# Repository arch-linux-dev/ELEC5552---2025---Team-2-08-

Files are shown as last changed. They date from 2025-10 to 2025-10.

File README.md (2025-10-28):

# ELEC5552 - 2025 - Team-2-08
Open-source Indoor Surveillance Drone by UWA Team 2-08 for ELEC5552. Includes hardware, firmware and software. Designed for safe indoor flight, testing, and future open-source development.

# FC
## Specifications
Two-layer custom Flight Controller PCB designed in Altium. Integrates ESP32-WROOM-32E microcontroller, ICM-42670P IMU, ultrasonic and IR sensor interfaces, and a 10-pin JST connector for ESC communication. Operates on 3.3 V logic and 5 V sensor input, with regulated power, compact form factor, and mounting compatibility with the drone chassis.
## Images


Top layer view of the Flight Controller PCB showing component layout and routing.



Bottom layer (ground plane) view showing grounding and power distribution.



3D rendered view of the completed Flight Controller PCB.

# ESC
## Specifications
Four-layer 4-in-1 Electronic Speed Controller (ESC) PCB integrating buck-boost and 3.3 V regulation stages, current-sense amplifier, STM32 microcontrollers, gate-driver ICs, and low R<sub>DS(on)</sub> MOSFETs for efficient BLDC motor control. Compatible with 1 S 3.7 V 800 mAh Li-Po battery and AM32 firmware. Designed for compactness, low noise, and safe integration within the quadcopter chassis.
## Images


Realistic top and bottom view of the ESC PCB showing component placement and overall layout.



Top, power, ground, and bottom plane views showing component layout and routing.

# Software
## Flight Controller PCB
The flight controller PCB, based on an ESP32 microcontroller with an inbuilt IMU and support for an attached time of flight, radar distance and optical flow sensor.
```
~/FC PCB - Altium Files/
```
The schematic and PCB were designed using Altium, and sent to PCBWay for maunfacturing.
## Electronic Speed Controller PCB
The ESC PCB, which is a four-in-one designed to power all motors of the quadcopter and regulate/distribute power to the flight controller and camera modules.
```
~/ESC PCB - Altium Files/
```
The motor channels are powered by STMicroelectronics MCUs and are intended to run AM32 ESC firmware.
## Flight Controller Firmware - Custom Version (retired)
The original flight controller firmware we intended to use, written in ESP-IDF for an ESP32 using FreeRTOS for scheduling.
```
~/FC Firmware - Version 1/
```
Communication over Wi-Fi using Websockets for data transfer. Complete with a web-based interface for piloting, adjusting PID parameters 'live' without re-writing firmware, and manually overriding setpoints and outputs.
This version was retired as the performance was not adequate for our liking.
## Flight Controller Firmware - Crazyflie Version
A revamped firmware package for our flight controller, this time based on the Crazyflie platform firmware ported to ESP32.
```
~/FC Firmware - Version 2/
```
This package was selected as it had pre-bundled drivers for our peripherals and a much more advanced arsenal of control loops, predictors and situational awareness handlers. 
Many functions were modified or replaced with custom versions to support our hardware and use case. Some of the larger changes include:
* The ESC communication is custom, and was written to translate Crazyflie's motor ratio (a value between 10000 and 60000) into a signal that BLHeli ESCs understand (pulse between 1000ms and 2000ms).
* The time-of-flight sensor drivers were modified to support the initialisation of a second device and address change of one of the devices so they can operate on the same bus simultaneously. 
## Ground Station Python Scripts
These files handle the autonomous navigation step-through, manual control takeover, and video recording via a laptop connected to the drone's Wi-Fi.
### Flight Planner and Manual Control
```
~/Ground Station/planner_interface.py
```
This script allows the planning of a flight path via mouse inputs, clicking points on a grid to set the x,y coordinates for the drone. It communicates these sequentially to the drone. There are also buttons to manually pilot the drone, and cut power when required.
### Video Recording
```
~/Ground Station/cam_handler.py
```
This script, upon launch, opens a stream from the ESP-CAM over the network and encodes it into a .avi file.

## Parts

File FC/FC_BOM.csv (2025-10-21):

Line # | Name | Description | Designator | Quantity | Manufacturer 1 | Manufacturer Part Number 1 | Footprint
 | CL10A226MQ8NRND | Cap Ceramic 22uF 6.3V X5R ±20% Pad SMD 0603 +85°C T/R | C1 | 1 | Samsung Electro-Mechanics | CL10A226MQ8NRND | FP-CL10-IPC_B
 | CAP 100nF 100V 0805(2012) | CAP 100nF 100V ±10% 0805 (2012 Metric) Thickness 1.45mm SMD | C2, C3, C5 | 3 | KEMET | C0805C104K1RACTU | CAPC0805(2012)145_M
 | CC0603KPX5R7BB225 | CC0603 2.2 uF X5R 10.00% 16 V | C6 | 1 | Yageo Group | CC0603KPX5R7BB225 | FP-CC0603-DA-MFG
 | 08056D106KAT4A |  | C7 | 1 | KYOCERA AVX | 08056D106KAT4A | CAPC2013X140X50ML20T25
 | ESP32-WROOM-32E-N8 | WiFi Modules - 802.11 SMD Module ESP32-WROOM-32E, ESP32-D0WD-V3, 8 MB SPI flash, PCB antenna | ESP32 | 1 | Espressif Systems | ESP32-WROOM-32E-N8 | ESP32WROOM32EN8
 | ICM-42670-P | Integrated Circuit | ICM | 1 | TDK | ICM-42670-P | ICM42670P
 | SM10B-SRSS-TB_LF__SN_ | Connector | J1 | 1 | JST | SM10B-SRSS-TB(LF)(SN) | SM10B-SRSS-TB
 | CES-104-02-S-S | Connector | J2, J4 | 2 | Samtec | CES-104-02-S-S | CES-104-XX-Y-S
 | CES-103-01-G-S | Connector | J3 | 1 | Samtec | CES-103-01-G-S | CES-103-XX-Y-S
 | CES-106-01-T-S | Connector | J5 | 1 | Samtec | CES-106-01-T-S | CES-106-XX-Y-S
 | 68001-204HLF | CONN HEADER VERT 4POS 2.54MM | JP1 | 1 | Amphenol Communications Solutions | 68001-204HLF | HDR Male1�~4 2.54mm
 | ERJ-3EKF2401V |  | R1, R4, R5 | 3 | Panasonic | ERJ-3EKF2401V | RESC1608X55X30ML15T15
 | AC0603JR-7W10KL | RES 10kO 5.00% 0.2W 0603 | R2, R3, R6 | 3 | Yageo Group | AC0603JR-7W10KL | FP-AC0603-IPC_A
 | RC1206FR-102KL |  | R7 | 1 | Yageo Group | RC1206FR-102KL | RESC3116X65X40ML10T20
 | RC1206JR-101KL |  | R8 | 1 | Yageo Group | RC1206JR-101KL | RESC3116X65X40ML10T20
 | TL3301AF160QG | SWITCH TACTILE SPST-NO 0.05A 12V | SW1 | 1 | E-Switch | TL3301AF160QG | FP-TL3301AF160QG-MFG
 | TXB0104D | IC TRNSLTR BIDIRECTIONAL 14SOIC | U1 | 1 | Texas Instruments | TXB0104D | FP-D0014A-IPC_A

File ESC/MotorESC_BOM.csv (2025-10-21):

Line # | Name | Description | Designator | Quantity | Manufacturer 1 | Manufacturer Part Number 1 | Supplier 1 | Supplier Part Number 1
 | TPS630701RNMR | IC REG BCK BST 5V 2A 15VQFN | U2 | 1 | Texas Instruments | TPS630701RNMR | Mouser | 595-TPS630701RNMR
 | TPS72733DSER | Single Output Fast Transient Response LDO, 250 mA, Fixed 3.3 V Output, 2 to 5.5 V Input, with Ultra-Low IQ, 6-pin WSON (DSE), -40 to 125 degC, Green (RoHS & no Sb/Br) | U1 | 1 | Texas Instruments | TPS72733DSER | Arrow Electronics | TPS72733DSER
 | T520A107M006ATE045 | CAP TANT POLY 100UF 6.3V 1206 | C26 | 1 | KEMET | T520A107M006ATE045 | Newark | 02AC0118
 | STM32G071GBU6 | IC MCU 32BIT 128KB FLSH 28UFQFPN | U3, U4, U28, U29 | 4 | STMicroelectronics | STM32G071GBU6 | Newark | 84AC2901
 | SM10B-SRSS-TB_LF__SN_ | Connector | J1 | 1 | JST | SM10B-SRSS-TB(LF)(SN) | Mouser | 306-SM10BSRSSTBLFSN
 | SIZ200DT-T1-GE3 | Dual N-Channel 30-V (D-S) MOSFETs Symm. PowerPAIR 3 x 3 1G sh ch , 5.5 m @ 10V m @ 7.5V 7.3 m @ 4.5V | Q1, Q2, Q3, Q4, Q5, Q6, Q7, Q8, Q9, Q10, Q11, Q12 | 12 | Vishay | SIZ200DT-T1-GE3 | Mouser | 78-SIZ200DT-T1-GE3
 | RM2012B-103103-PBVW10 | No Description Available | R12, R13, R24, R25 | 4 | Susumu | RM2012B-103/103-PBVW10 | DigiKey | RM20B10K/10KPCT-ND
 | NCP81161MNTBG | No Description Available | U5, U6, U12, U13, U24, U25, U30, U31, U32, U33, U34, U35 | 12 | onsemi | NCP81161MNTBG | DigiKey | NCP81161MNTBGOSCT-ND
 | MCS04020C1001FE000 | RES SMD 1.2K OHM 1% 1/10W 0402 | R1 | 1 | Vishay | MCS04020C1001FE000 | Newark | 65AC3521
 | INA186A2IDCKT | IC CURR SENSE 1 CIRCUIT SC70-6 | U9 | 1 | Texas Instruments | INA186A2IDCKT | Mouser | 595-INA186A2IDCKT
 | HSMW-C191 |  | D1 | 1 | Avago | HSMW-C191 | Farnell | 1058375
 | HCS1206FTL500 | RES SHUNT, 1206, 0.0005 ohm, 1%, 2W | R9 | 1 | Stackpole Electronics | HCS1206FTL500 | Mouser | 708-HCS1206FTL500
 | GRM188R61E106KA73J | Chip Multilayer Ceramic Capacitors for General Purpose, 0603, 10uF, X5R, 15%, 10%, 25V | C28, C29 | 2 | Murata | GRM188R61E106KA73J | Mouser | 81-GRM188R61E106KA3J
 | GRM155R61A106ME11D | Chip Multilayer Ceramic Capacitors for General Purpose, 0402, 10uF, X5R, 15%, 20%, 10V | C9, C10, C34, C35, C41, C43, C47, C48, C55, C57, C61, C62 | 12 | Murata | GRM155R61A106ME11D | Mouser | 81-GRM155R61A106ME1D
 | GRM21BR61E106MA73L | Chip Multilayer Ceramic Capacitors for General Purpose, 0805, 10uF, X5R, 15%, 20%, 25V | C27 | 1 | Murata | GRM21BR61E106MA73L | Mouser | 81-GRM21BR61E106MA3L
 | GCJ188R71C104MA01D | Cap Ceramic 0.1uF 16V X7R 20% Pad SMD 0603 Soft Termination +125°C Automotive T/R | C31, C32, C39, C40, C45, C46, C53, C54, C59, C60, C65, C66 | 12 | Murata | GCJ188R71C104MA01D | Mouser | 81-GCJ188R71C104MA1D
 | EXB24V102JX | No Description Available | U7, U8, U10, U11 | 4 | Panasonic | EXB-24V102JX | DigiKey | Y5102CT-ND
 | EXB24V100JX | No Description Available | U14, U15, U16, U17, U18, U19, U20, U21, U22, U23, U26, U27 | 12 | Panasonic | EXB-24V100JX | DigiKey | Y5100CT-ND
 | DFE252012F-R82M=P2 | Shielded Wirewound Inductor 0.82uH 20% 3600mA 0.035O 1008 (2520) | L1 | 1 | Murata | DFE252012F-R82M=P2 | Arrow Electronics | DFE252012F-R82M=P2
 | CRG0402F10K | RES SMD 10K OHM 1% 1/16W 0402 | R8, R10, R11, R22, R23 | 5 | TE Connectivity | CRG0402F10K | Newark | 95W7406
 | CAP 10uF 16V 1206(3216) | CAP 10uF 16V -20% to +80% 1206 (3216 Metric) Thickness 1.9mm SMD | C17 | 1 | Yageo Group | CC1206ZKY5V7BB106 | Mouser | 603-CC126ZKY5V7BB106
 | CC0805MKX5R8BB226 | CAP CER 22UF 25V X5R 0805 | C1, C2, C3, C5, C6, C7, C8, C18, C19, C20, C21, C22, C23, C24, C25 | 15 | Yageo Group | CC0805MKX5R8BB226 | Mouser | 603-CC805MKX5R8BB226
 | CAY10-222J4LF | No Description Available | R14, R15, R26, R27 | 4 | Bourns | CAY10-222J4LF | Avnet | 06X4909
 | C0402C103K5RACTU | CAP CER 10000PF 50V X7R 0402 | C38 | 1 | KEMET | C0402C103K5RACTU | Mouser | 80-C0402C103K5R
 | BLM18SG221TN1D | Chip Ferrite Bead, 0603, 220O @ 100MHz, 25%, 0.04O, 2.5A | FB1, FB2 | 2 | Murata | BLM18SG221TN1D | Mouser | 81-BLM18SG221TN1D
 | AC0402FR-7W4K7L | RES 4.7kO ±1% 0.125W 0402 | R2, R3, R4, R5, R6, R7, R16, R17, R18, R19, R20, R21 | 12 | Yageo Group | AC0402FR-7W4K7L | Newark | 59AK0904
 | 12101C225KAZ2A | General Purpose Ceramic Capacitor, 1210, 2.2uF, 10%, X7R, 15%, 100V | C15, C16 | 2 | KYOCERA AVX | 12101C225KAZ2A | Mouser | 581-12101C225KAZ2A
 | 9931-0-00-15-00-00-03-0 | Circuit Board Hardware - PCB STANDARD I.C. PIN | J3, J4, J5, J6, J7, J8, J9, J10, J11, J12, J13, J14 | 12 | Mill-Max | 9931-0-00-15-00-00-03-0 | Mouser | 575-993100150030
 | CAP 100nF 25V 0402(1005) | CAP 100nF 25V ±20% 0402 (1005 Metric) Thickness 0.6mm SMD | C30, C33 | 2 | KYOCERA AVX | 04023D104MAT2A | Mouser | 581-04023D104MAT2A
 | 04023C104JAT2A |  | C11, C12, C13, C14, C36, C37, C42, C44, C49, C50, C51, C52, C56, C58, C63, C64 | 16 | KYOCERA AVX | 04023C104JAT2A | Newark | 96Y8155
 | 741X043222JP | Resistor Networks & Arrays 2.2Kohms 5% Isolated | X1, X2, X3, X4 | 4 | CTS Components | 741X043222JP | Mouser | 774-741X043222JP

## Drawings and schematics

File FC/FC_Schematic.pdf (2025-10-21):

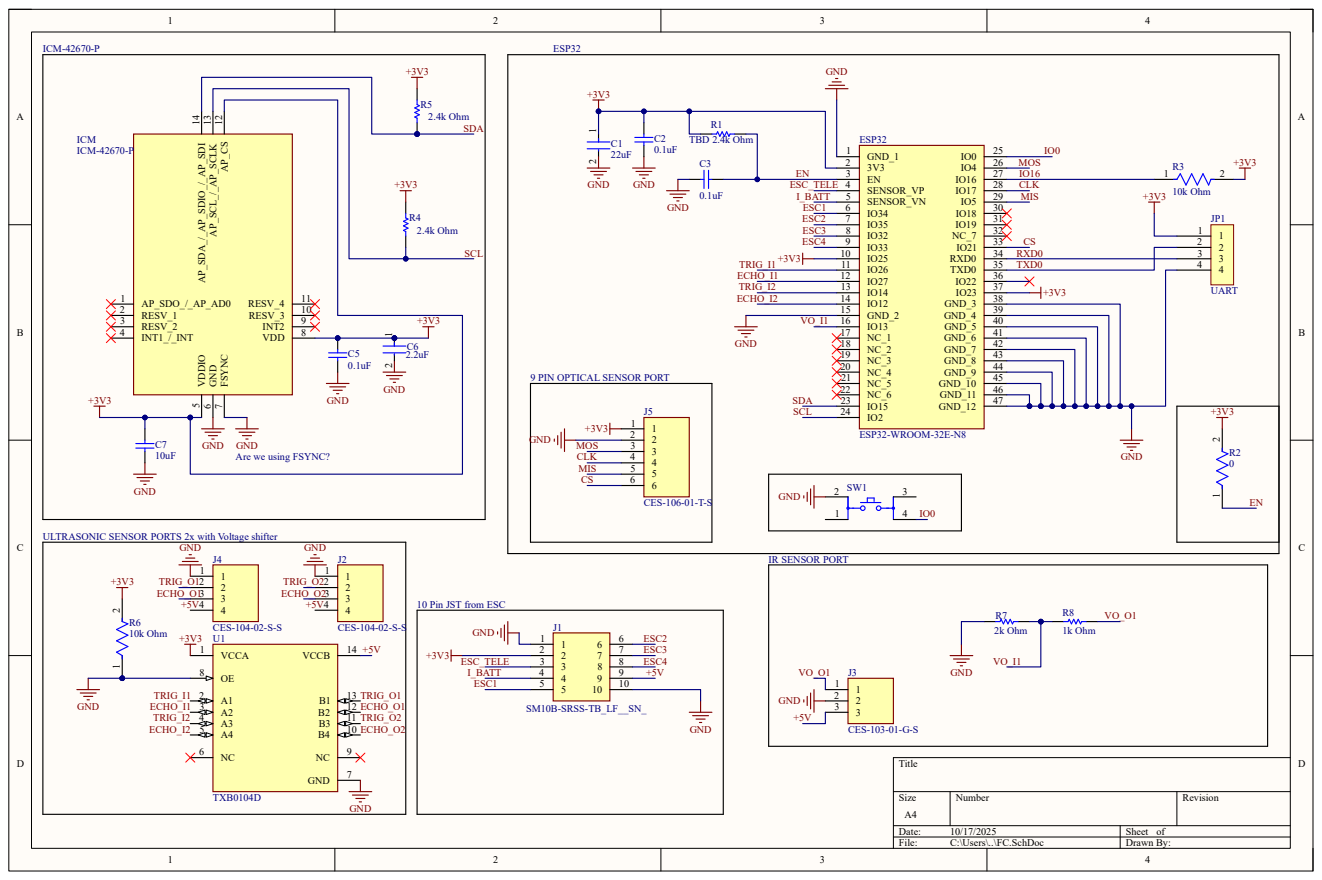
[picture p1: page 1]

9 PIN OPTICAL SENSOR PORT

GND
Are we using FSYNC?

ULTRASONIC SENSOR PORTS 2x with Voltage shifter

10 Pin JST from ESC

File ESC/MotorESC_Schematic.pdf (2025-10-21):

Decoupling Capacitors | Buck-Boost Converter

# GND¹ ²

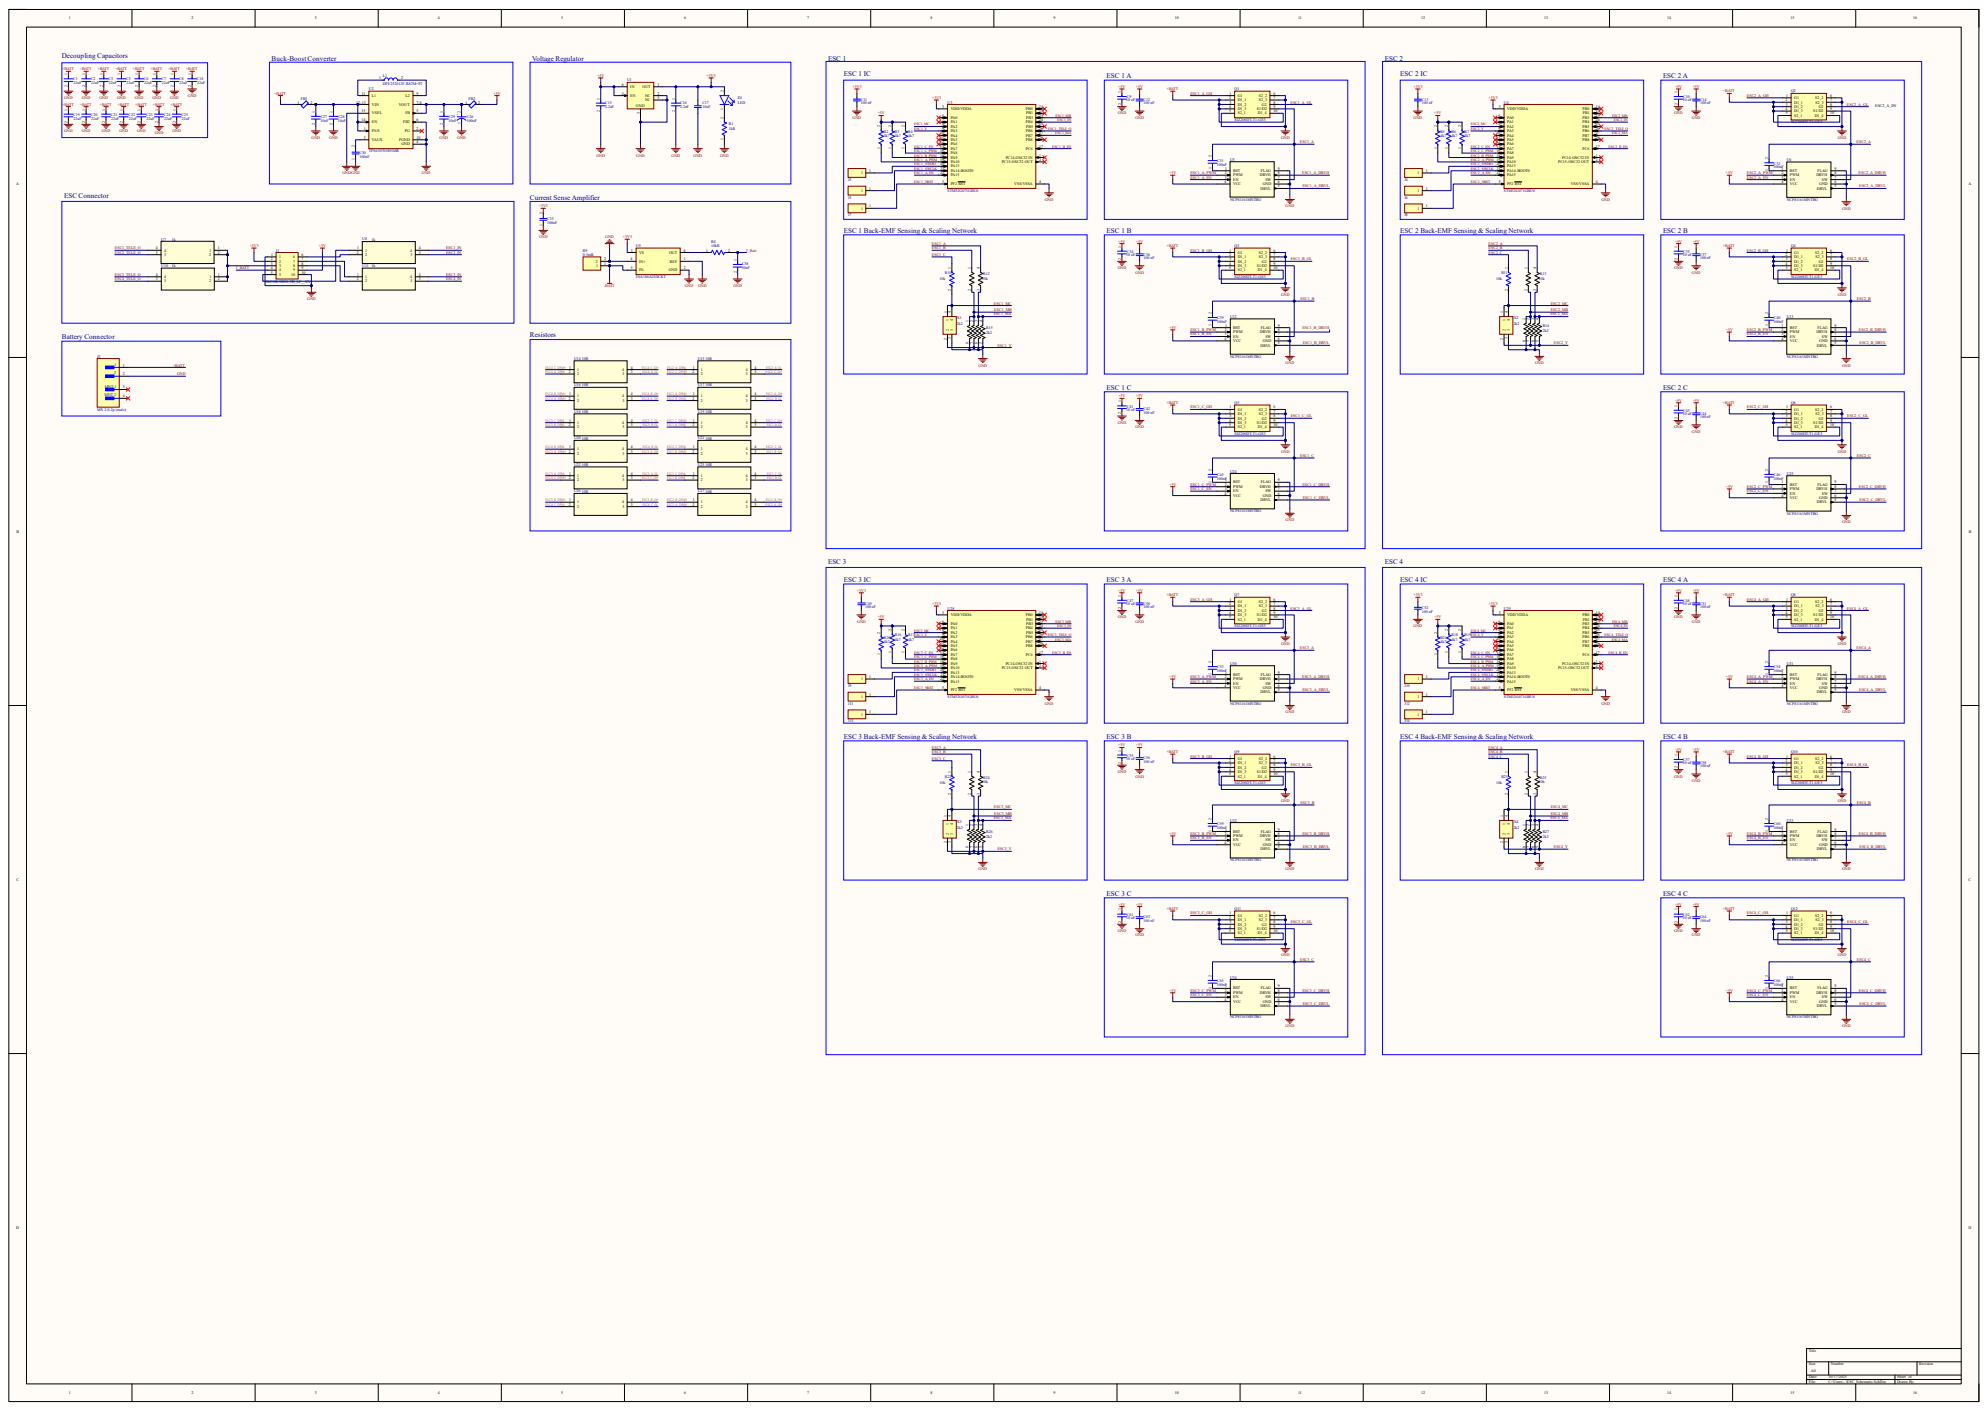
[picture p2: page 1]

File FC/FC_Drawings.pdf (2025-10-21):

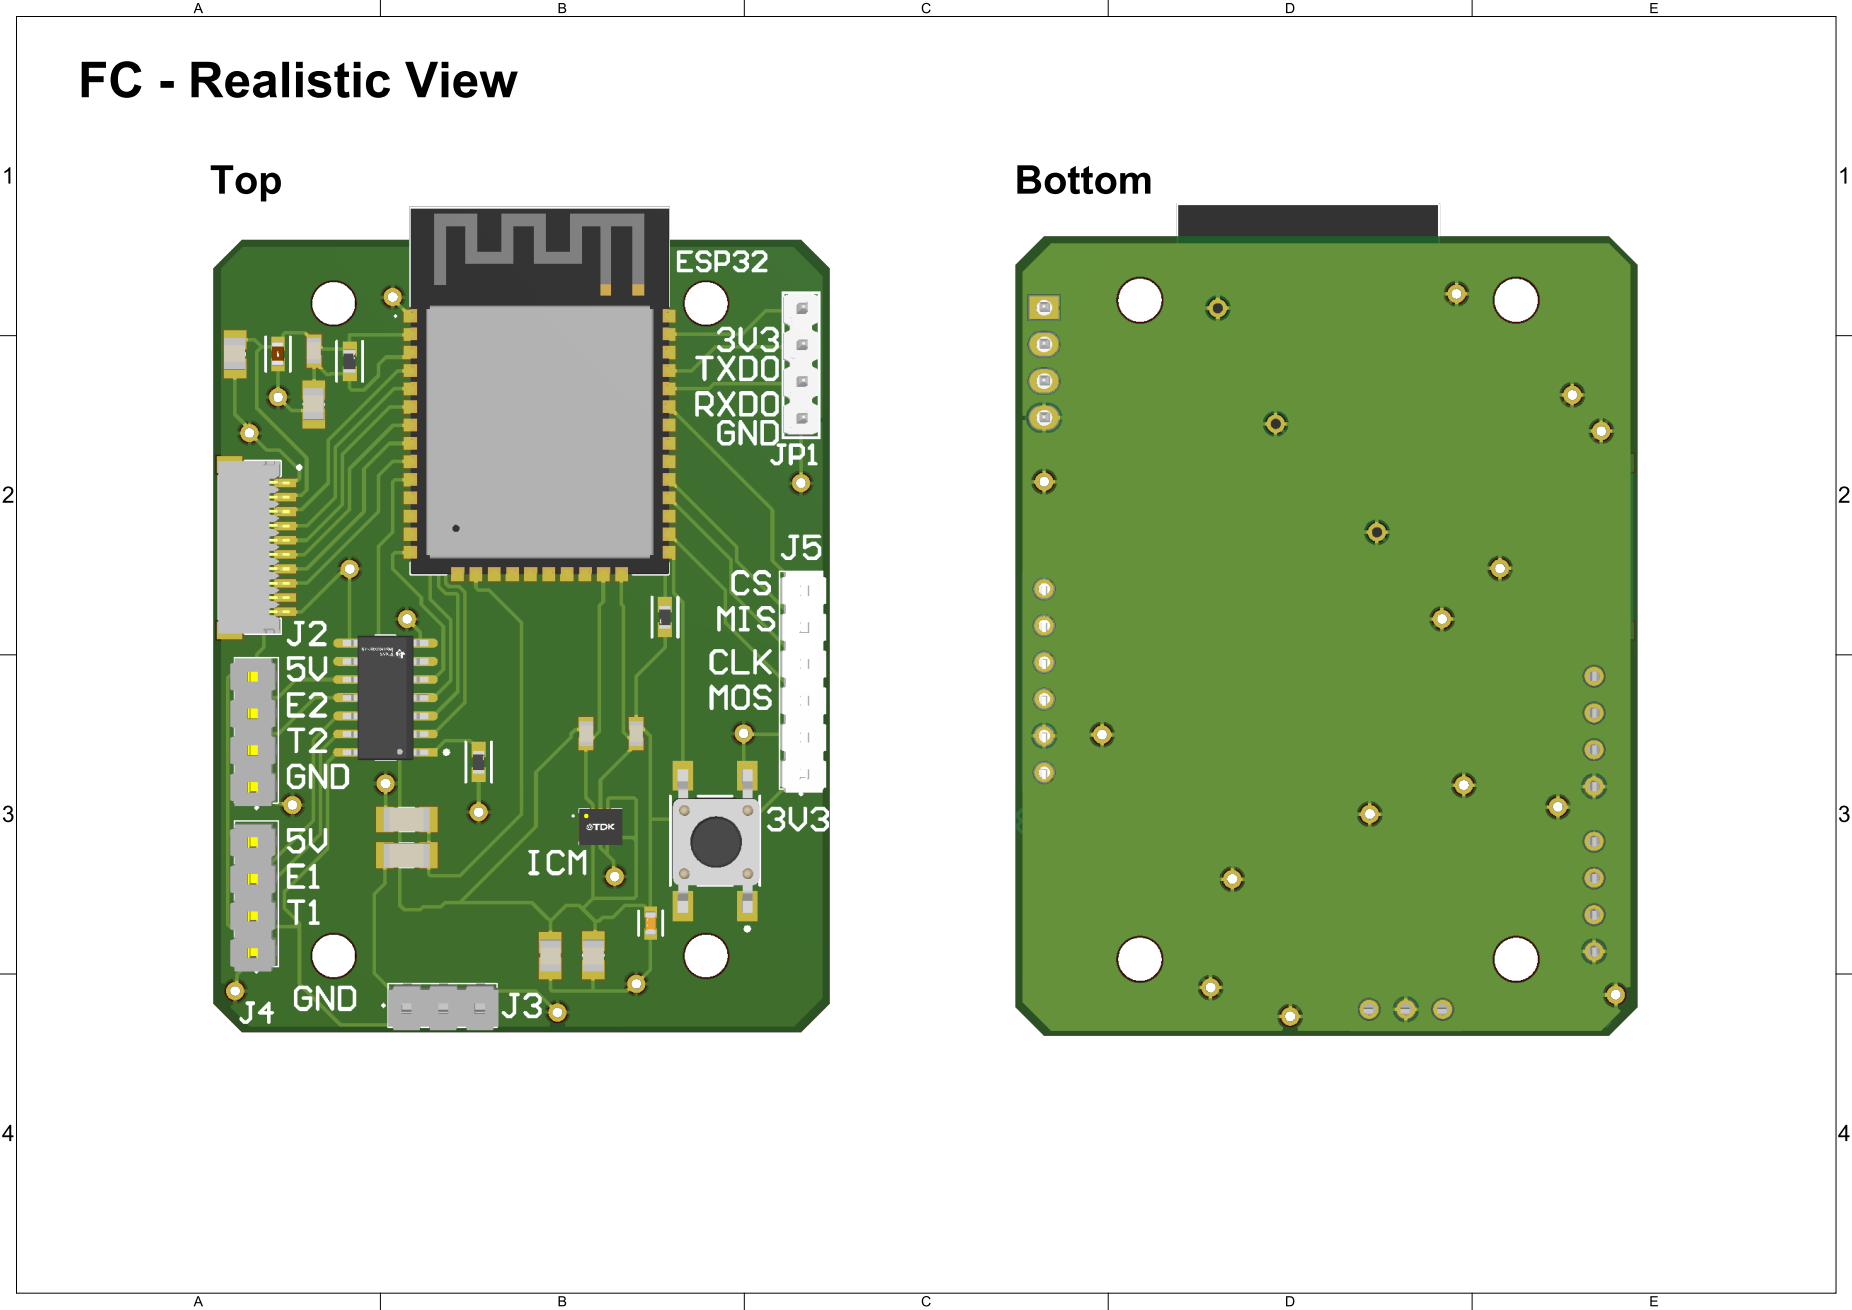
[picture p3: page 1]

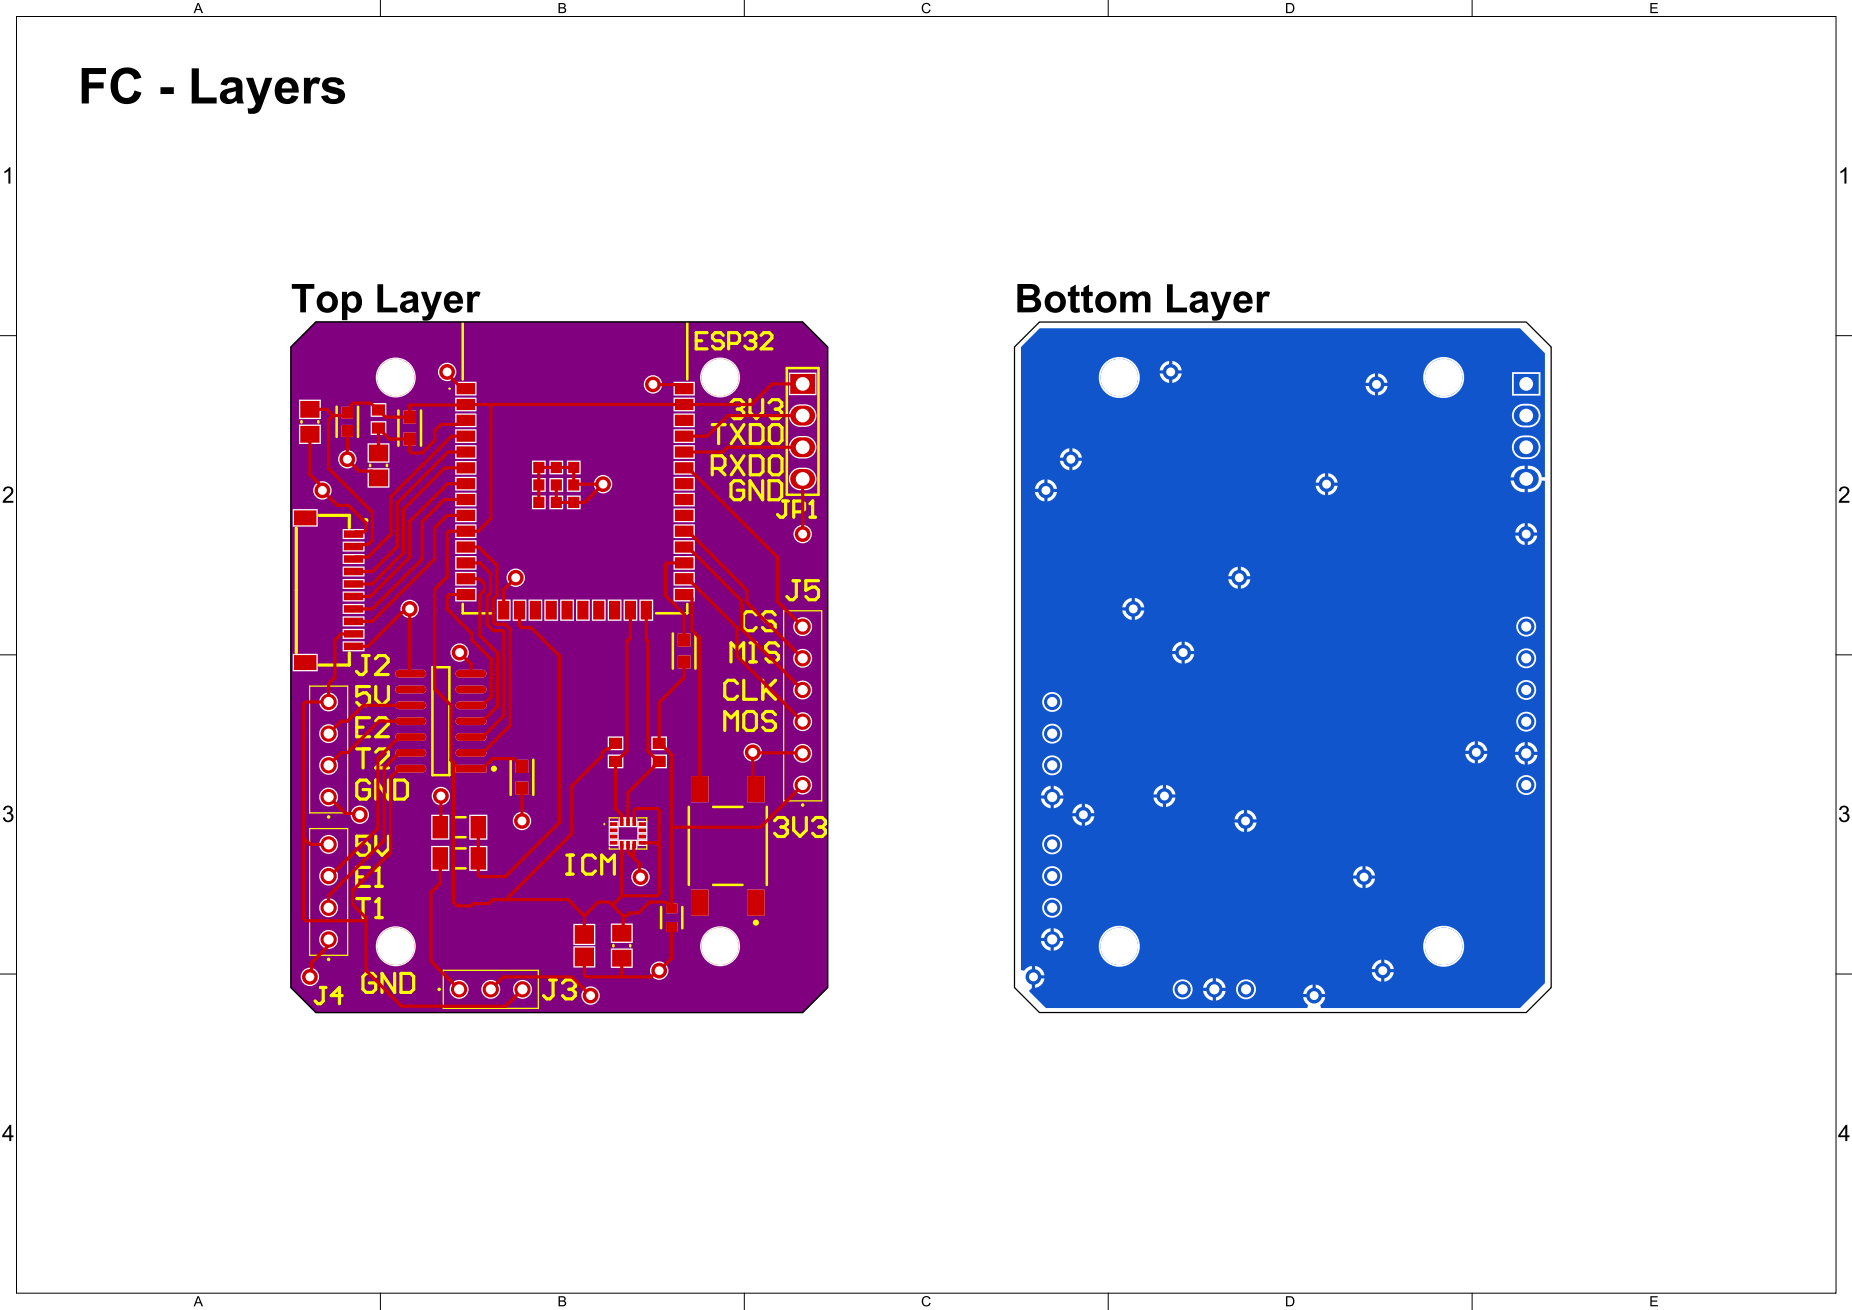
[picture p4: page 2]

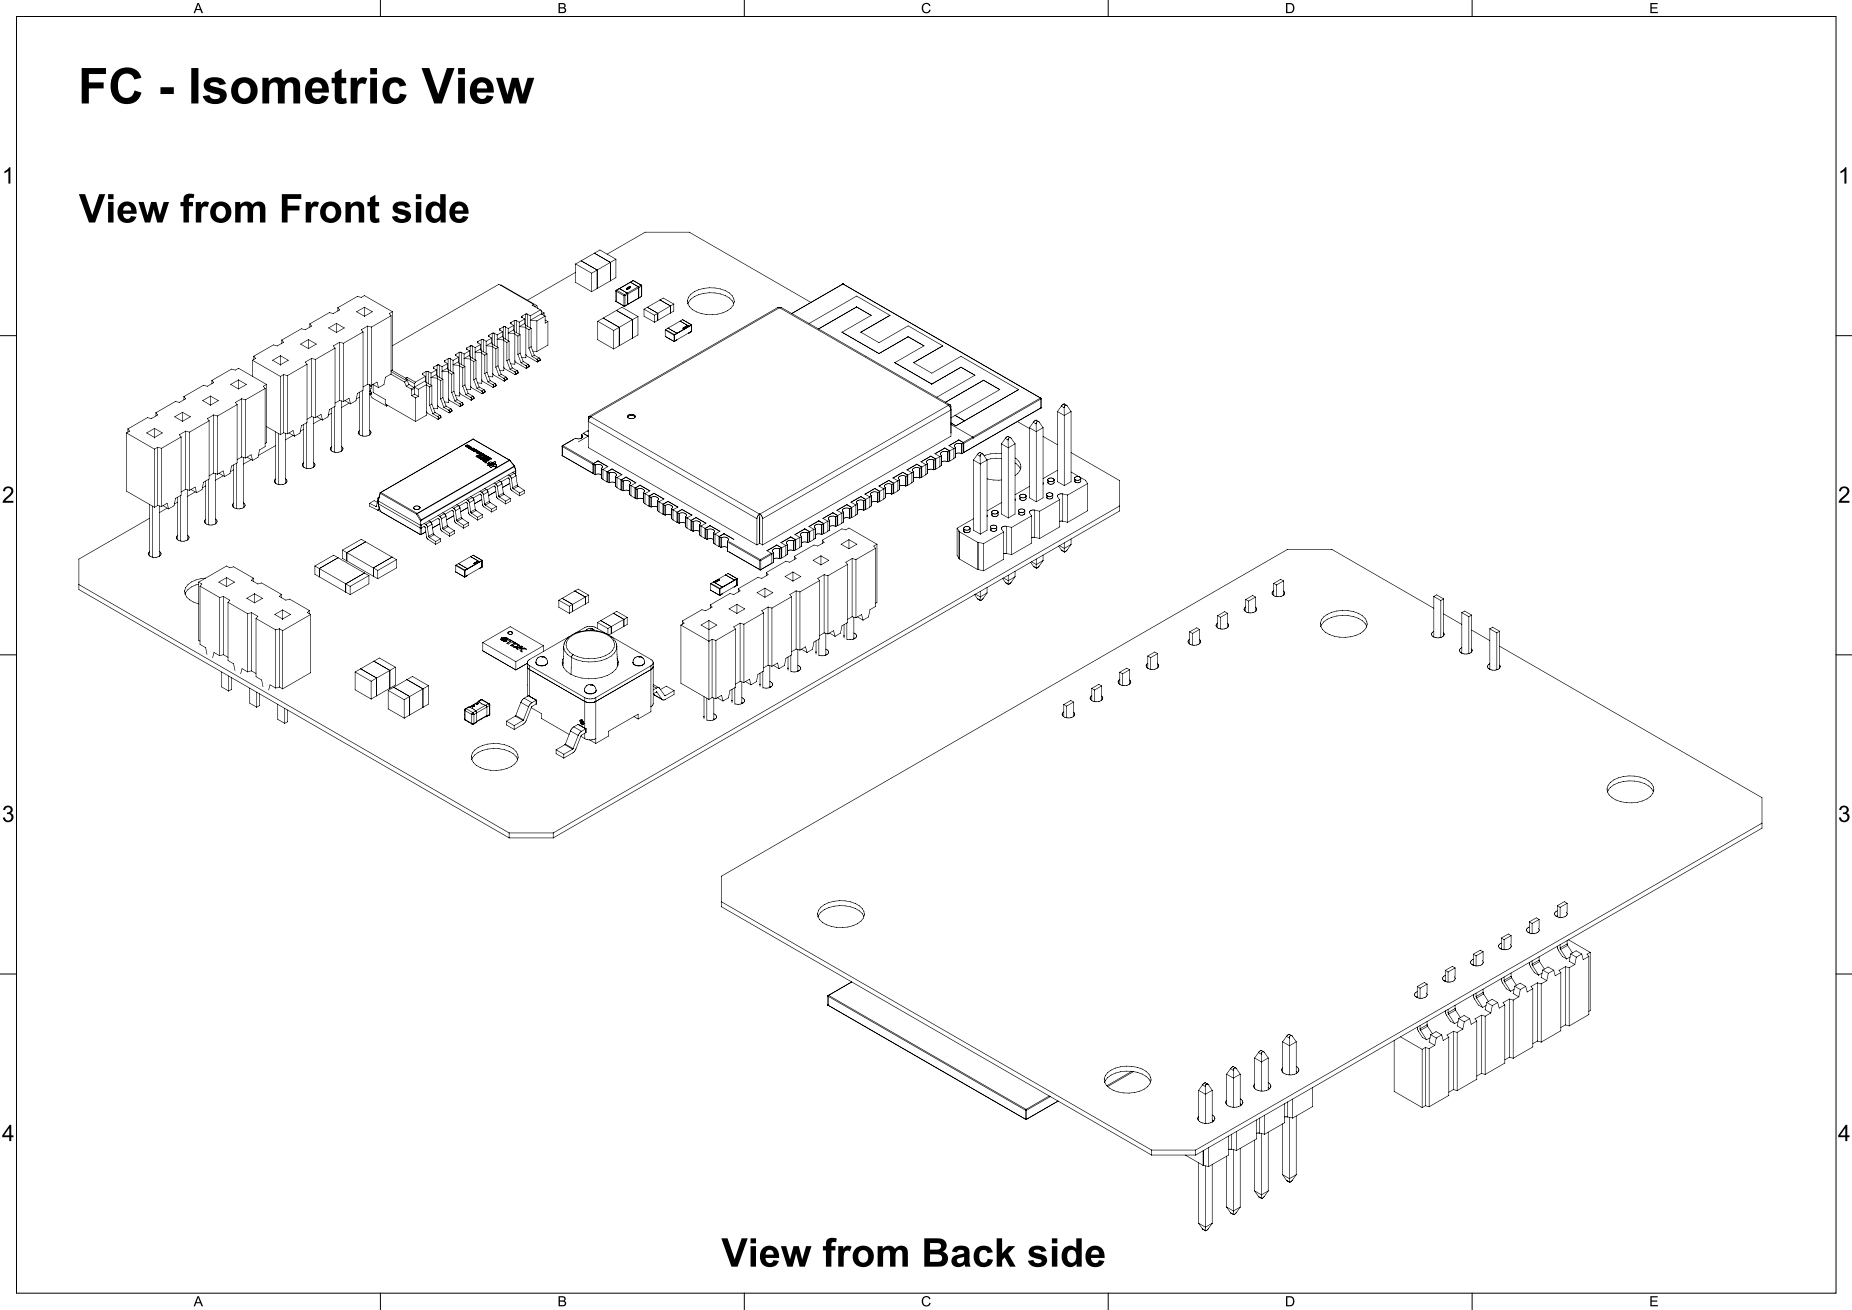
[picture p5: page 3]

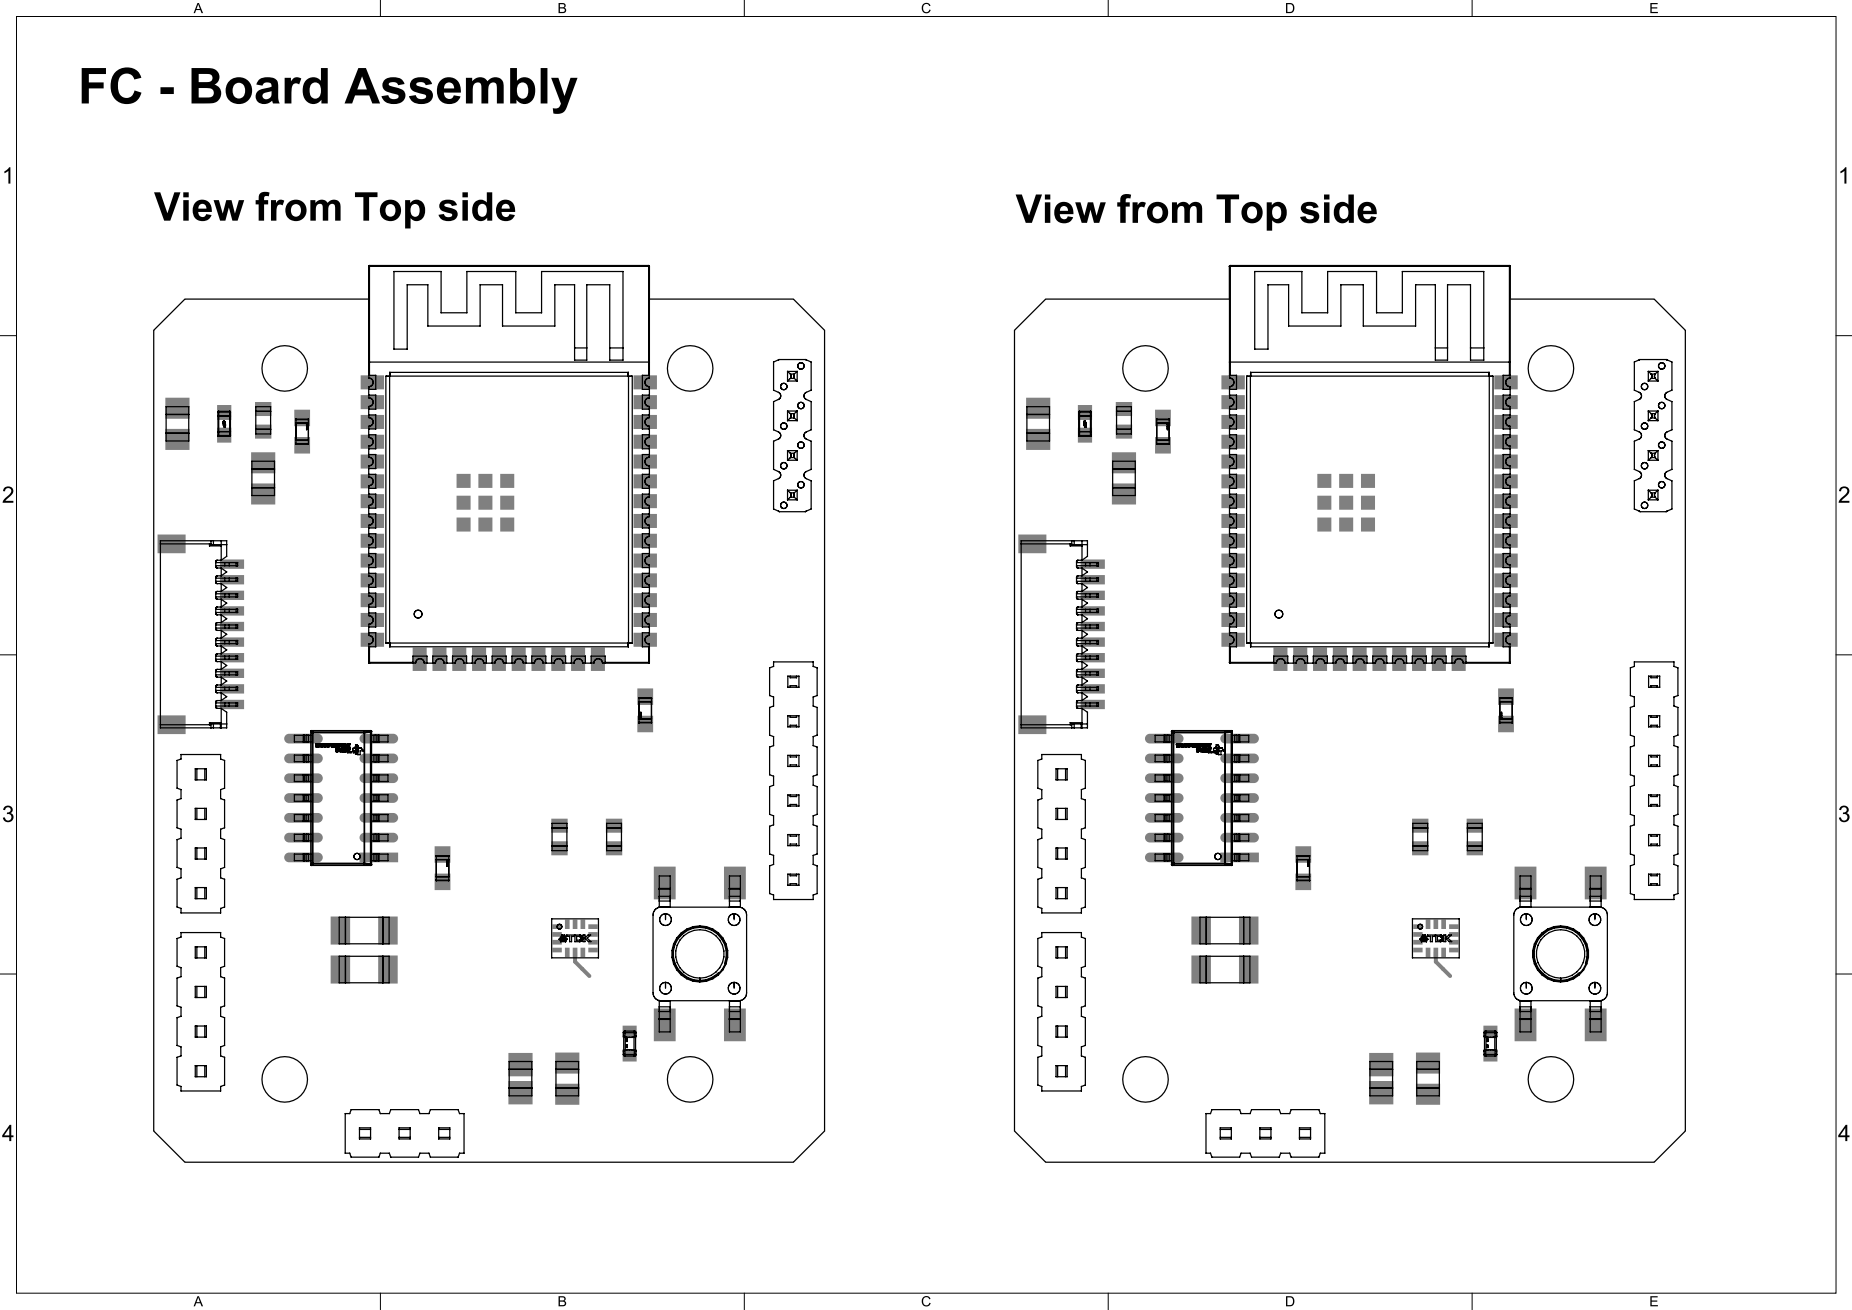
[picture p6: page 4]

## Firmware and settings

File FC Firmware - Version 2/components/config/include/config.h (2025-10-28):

/**
 *
 * ESP-Drone Firmware
 * 
 * Copyright 2019-2020  Espressif Systems (Shanghai) 
 * Copyright (C) 2011-2012 Bitcraze AB
 *
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
 * config.h - Main configuration file
 *
 * This file define the default configuration of the copter
 * It contains two types of parameters:
 * - The global parameters are globally defined and independent of any
 *   compilation profile. An example of such define could be some pinout.
 * - The profiled defines, they are parameter that can be specific to each
 *   dev build. The vanilla build is intended to be a "customer" build without
 *   fancy spinning debugging stuff. The developers build are anything the
 *   developer could need to debug and run his code/crazy stuff.
 *
 * The golden rule for the profile is NEVER BREAK ANOTHER PROFILE. When adding a
 * new parameter, one shall take care to modified everything necessary to
 * preserve the behavior of the other profiles.
 *
 * For the flag. T_ means task. H_ means HAL module. U_ would means utils.
 */

#ifndef CONFIG_H_
#define CONFIG_H_
//#include "nrf24l01.h"

//#include "trace.h"
#include "usec_time.h"
#include "sdkconfig.h"

#define PROTOCOL_VERSION 4
#define QUAD_FORMATION_X

#ifdef CONFIG_TARGET_ESPLANE_V2_S2
#ifndef CONFIG_IDF_TARGET_ESP32S2
#error "ESPLANE_V2 hardware with ESP32S2 onboard"
#endif
#elif defined(CONFIG_TARGET_ESPLANE_V1)
#ifndef CONFIG_IDF_TARGET_ESP32
#error "ESPLANE_V1 hardware with ESP32 onboard"
#endif
#elif defined(CONFIG_TARGET_ESP32_S2_DRONE_V1_2)
#ifdef CONFIG_IDF_TARGET_ESP32
#error "ESP32_S2_DRONE_V1_2 hardware with ESP32S2/S3 onboard"
#endif
#endif

#ifdef STM32F4XX 
  #define CONFIG_BLOCK_ADDRESS    (2048 * (64-1))
  #define MCU_ID_ADDRESS          0x1FFF7A10
  #define MCU_FLASH_SIZE_ADDRESS  0x1FFF7A22
  #ifndef FREERTOS_HEAP_SIZE
    #define FREERTOS_HEAP_SIZE      20000
  #endif
  #define FREERTOS_MIN_STACK_SIZE 150       // M4-FPU register setup is bigger so stack needs to be bigger
  #define FREERTOS_MCU_CLOCK_HZ   168000000

  #define configGENERATE_RUN_TIME_STATS 1
  #define portCONFIGURE_TIMER_FOR_RUN_TIME_STATS() initUsecTimer()
  #define portGET_RUN_TIME_COUNTER_VALUE() usecTimestamp()
#endif


//#define DEBUG_UDP
//#define DEBUG_EP2

// Task priorities. Higher number higher priority
// system state tasks
#define SYSTEM_TASK_PRI         1
#define PM_TASK_PRI             1
#define LEDSEQCMD_TASK_PRI      1
// communication TX tasks
#define UDP_TX_TASK_PRI         2
#define CRTP_TX_TASK_PRI        2
// communication RX tasks
#define UDP_RX_TASK_PRI         2
#define EXTRX_TASK_PRI          2
#define UART2_TASK_PRI          2
#define SYSLINK_TASK_PRI        2
#define USBLINK_TASK_PRI        2
#define WIFILINK_TASK_PRI       2
#define CRTP_RX_TASK_PRI        2
#define CMD_HIGH_LEVEL_TASK_PRI 3
#define INFO_TASK_PRI           2
#define LOG_TASK_PRI            2
#define MEM_TASK_PRI            2
#define PARAM_TASK_PRI          2
// sensors and stabilize related tasks
#define PROXIMITY_TASK_PRI      5
#define FLOW_TASK_PRI           5
#define ZRANGER2_TASK_PRI       5
#define ZRANGER_TASK_PRI        5
#define SENSORS_TASK_PRI        6
#define STABILIZER_TASK_PRI     7
#define KALMAN_TASK_PRI         4

// the kalman filter consumes a lot of CPU
// for single core systems, we need to lower the priority
#if CONFIG_FREERTOS_UNICORE
  #undef KALMAN_TASK_PRI
  #define KALMAN_TASK_PRI         1
#endif

// Task names
#define CMD_HIGH_LEVEL_TASK_NAME "CMDHL"
#define CRTP_RX_TASK_NAME       "CRTP-RX"
#define CRTP_TX_TASK_NAME       "CRTP-TX"
#define EXTRX_TASK_NAME         "EXTRX"
#define FLOW_TASK_NAME          "FLOW"
#define KALMAN_TASK_NAME        "KALMAN"
#define LEDSEQCMD_TASK_NAME     "LEDSEQCMD"
#define LOG_TASK_NAME           "LOG"
#define MEM_TASK_NAME           "MEM"
#define PARAM_TASK_NAME         "PARAM"
#define PM_TASK_NAME            "PWRMGNT"
#define PROXIMITY_TASK_NAME     "PROXIMITY"
#define SENSORS_TASK_NAME       "SENSORS"
#define STABILIZER_TASK_NAME    "STABILIZER"
#define SYSLINK_TASK_NAME       "SYSLINK"
#define SYSTEM_TASK_NAME        "SYSTEM"
#define UART2_TASK_NAME         "UART2"
#define UDP_RX_TASK_NAME        "UDP_RX"
#define UDP_TX_TASK_NAME        "UDP_TX"
#define USBLINK_TASK_NAME       "USBLINK"
#define WIFILINK_TASK_NAME      "WIFILINK"
#define ZRANGER2_TASK_NAME      "ZRANGER2"
#define ZRANGER_TASK_NAME       "ZRANGER"
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

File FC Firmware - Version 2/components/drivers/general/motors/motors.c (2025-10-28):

/**
 *
 * ESP-Drone Firmware
 *
 * Copyright 2019-2020  Espressif Systems (Shanghai)
 * Copyright (C) 2011-2012 Bitcraze AB
 *
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
 * motors.c - Motor driver
 *
 */

#include <stdbool.h>

//FreeRTOS includes
#include "freertos/FreeRTOS.h"
#include "freertos/task.h"

#include "stm32_legacy.h"
#include "motors.h"
#include "pm_esplane.h"
#include "log.h"
#define DEBUG_MODULE "MOTORS"
#include "debug_cf.h"

static uint16_t motorsConvBitsTo16(uint16_t bits);
static uint16_t motorsConv16ToBits(uint16_t bits);

uint32_t motor_ratios[] = {0, 0, 0, 0};

void motorsPlayTone(uint16_t frequency, uint16_t duration_msec);
void motorsPlayMelody(uint16_t *notes);
void motorsBeep(int id, bool enable, uint16_t frequency, uint16_t ratio);

const MotorPerifDef **motorMap; /* Current map configuration */

const uint32_t MOTORS[] = {MOTOR_M1, MOTOR_M2, MOTOR_M3, MOTOR_M4};

const uint16_t testsound[NBR_OF_MOTORS] = {A4, A5, F5, D5};

static bool isInit = false;
static bool isTimerInit = false;

ledc_channel_config_t motors_channel[NBR_OF_MOTORS] = {
    {
        .channel = MOT_PWM_CH1,
        .duty = 0,
        .gpio_num = MOTOR1_GPIO,
        .speed_mode = LEDC_LOW_SPEED_MODE,
        .timer_sel = LEDC_TIMER_0
    },
    {
        .channel = MOT_PWM_CH2,
        .duty = 0,
        .gpio_num = MOTOR2_GPIO,
        .speed_mode = LEDC_LOW_SPEED_MODE,
        .timer_sel = LEDC_TIMER_0
    },
    {
        .channel = MOT_PWM_CH3,
        .duty = 0,
        .gpio_num = MOTOR3_GPIO,
        .speed_mode = LEDC_LOW_SPEED_MODE,
        .timer_sel = LEDC_TIMER_0
    },
    {
        .channel = MOT_PWM_CH4,
        .duty = 0,
        .gpio_num = MOTOR4_GPIO,
        .speed_mode = LEDC_LOW_SPEED_MODE,
        .timer_sel = LEDC_TIMER_0
    },
};
/* Private functions */

static uint16_t motorsConvBitsTo16(uint16_t bits)
{
    return ((bits) << (16 - MOTORS_PWM_BITS));
}

static uint16_t motorsConv16ToBits(uint16_t bits)
{

    //return ((bits) >> (16 - MOTORS_PWM_BITS) & ((1 << MOTORS_PWM_BITS) - 1));
    float convbit = 128.0f + (bits - 10000.0f) * (128.0f / (65536.0f - 10000.0f));
    if (convbit < 128) convbit = 128; //clamp to min value to keep ESCs armed
    if (convbit > 256) convbit = 256; //max motor speed for testing
    return (uint32_t)convbit;
}

bool pwm_timmer_init()
{
    if (isTimerInit) {
        // First to init will configure it
        return TRUE;
    }

    /*
     * Prepare and set configuration of timers
     * that will be used by MOTORS Controller
     */
    ledc_timer_config_t ledc_timer = {
        .duty_resolution = MOTORS_PWM_BITS, // resolution of PWM duty
        .freq_hz = 500,					// frequency of PWM signal
        .speed_mode = LEDC_LOW_SPEED_MODE, // timer mode
        .timer_num = LEDC_TIMER_0,			// timer index
        // .clk_cfg = LEDC_AUTO_CLK,              // Auto select the source clock
    };

    // Set configuration of timer0 for high speed channels
    if (ledc_timer_config(&ledc_timer) == ESP_OK) {
        isTimerInit = TRUE;
        return TRUE;
    }

    return FALSE;
}

/* Public functions */

void arm_bldc(void){
    DEBUG_PRINTI("ESC Arming sequence in progress\n");
    for (int i = 0; i < NBR_OF_MOTORS; i++) {
        uint16_t ratio = 32768;
        DEBUG_PRINTI("Setting arm pulse on ESC %i for %i\n", i, (uint32_t)motorsConv16ToBits(ratio));
        ledc_set_duty(motors_channel[i].speed_mode, motors_channel[i].channel, 128); // hardcoded for 1000us on 50Hz PWM
        ledc_update_duty(motors_channel[i].speed_mode, motors_channel[i].channel);    }

     vTaskDelay(M2T(5000));

     // Quick spin up test
        for (int i = 0; i < NBR_OF_MOTORS; i++) {
        uint16_t ratio = 38667;
        DEBUG_PRINTI("Testing pulse on ESC %i for %i\n", i, (uint32_t)motorsConv16ToBits(ratio));
        ledc_set_duty(motors_channel[i].speed_mode, motors_channel[i].channel, 180); // hardcoded for 1000us on 50Hz PWM
        ledc_update_duty(motors_channel[i].speed_mode, motors_channel[i].channel); 
        vTaskDelay(M2T(200));
        ledc_set_duty(motors_channel[i].speed_mode, motors_channel[i].channel, 128); // hardcoded for 1000us on 50Hz PWM
        ledc_update_duty(motors_channel[i].speed_mode, motors_channel[i].channel);
    }
        

    DEBUG_PRINTI("ESC Arm pulse send complete\n");

}

//Initialization. Will set all motors ratio to 0%
void motorsInit(const MotorPerifDef **motorMapSelect)
{
    int i;

    if (isInit) {
        // First to init will configure it
        return;
    }

    motorMap = motorMapSelect;

    if (pwm_timmer_init() != TRUE) {
        return;
    }

    for (i = 0; i < NBR_OF_MOTORS; i++) {
        ledc_channel_config(&motors_channel[i]);
    }

    arm_bldc();
    isInit = true;
}


void motorsDeInit(const MotorPerifDef **motorMapSelect)
{
    for (int i = 0; i < NBR_OF_MOTORS; i++) {
        ledc_stop(motors_channel[i].speed_mode, motors_channel[i].channel, 0);
    }
}

bool motorsTest(void)
{
    int i;

    for (i = 0; i < sizeof(MOTORS) / sizeof(*MOTORS); i++) {
        if (motorMap[i]->drvType == BRUSHED) {
#ifdef ACTIVATE_STARTUP_SOUND
            //motorsBeep(MOTORS[i], true, testsound[i], (uint16_t)(MOTORS_TIM_BEEP_CLK_FREQ / A4) / 20);
            //vTaskDelay(M2T(MOTORS_TEST_ON_TIME_MS));
            //motorsBeep(MOTORS[i], false, 0, 0);
            //vTaskDelay(M2T(MOTORS_TEST_DELAY_TIME_MS));
#else
            //motorsSetRatio(MOTORS[i], MOTORS_TEST_RATIO);
            //vTaskDelay(M2T(MOTORS_TEST_ON_TIME_MS));
            //motorsSetRatio(MOTORS[i], 0);
            //vTaskDelay(M2T(MOTORS_TEST_DELAY_TIME_MS));
#endif
        }
    }

    return isInit;
}

// Ithrust is thrust mapped for 65536 <==> 60 grams
void motorsSetRatio(uint32_t id, uint16_t ithrust)
{
    if (isInit) {
        uint16_t ratio;

        ASSERT(id < NBR_OF_MOTORS);

        ratio = ithrust;

#ifdef ENABLE_THRUST_BAT_COMPENSATED

        if (motorMap[id]->drvType == BRUSHED) {
            float thrust = ((float)ithrust / 65536.0f) * 40; //根据实际重量修改
            float volts = -0.0006239f * thrust * thrust + 0.088f * thrust;
            float supply_voltage = pmGetBatteryVoltage();
            float percentage = volts / supply_voltage;
            percentage = percentage > 1.0f ? 1.0f : percentage;
            ratio = percentage * UINT16_MAX;
            motor_ratios[id] = ratio;
        }

#endif
        ledc_set_duty(motors_channel[id].speed_mode, motors_channel[id].channel, (uint32_t)motorsConv16ToBits(ratio));
        DEBUG_PRINTI("Set ratio to %i", (uint32_t)motorsConv16ToBits(ratio));
        ledc_update_duty(motors_channel[id].speed_mode, motors_channel[id].channel);
        motor_ratios[id] = ratio;
#ifdef DEBUG_EP2
        DEBUG_PRINT_LOCAL("motors ID = %d ,ithrust_10bit = %d", id, (uint32_t)motorsConv16ToBits(ratio));
#endif
    }
}
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

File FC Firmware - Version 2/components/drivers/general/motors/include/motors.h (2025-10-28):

/**
 *
 * ESP-Drone Firmware
 *
 * Copyright 2019-2020  Espressif Systems (Shanghai)
 * Copyright (C) 2011-2012 Bitcraze AB
 *
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
 * Motors.h - Motor driver header file
 *
 */
#ifndef __MOTORS_H__
#define __MOTORS_H__

#include <stdint.h>
#include <stdbool.h>

#include "driver/ledc.h"

#include "config.h"
#include "stm32_legacy.h"


/******** Defines ********/

// CF2 PWM ripple is filtered better at 328kHz. At 168kHz the NCP702 regulator is affected.

#define MOTORS_PWM_BITS           LEDC_TIMER_8_BIT
#define MOTORS_PWM_PERIOD         ((1<<MOTORS_PWM_BITS) - 1)
#define MOTORS_TIM_BEEP_CLK_FREQ  4000000

// Compensate thrust depending on battery voltage so it will produce about the same
// amount of thrust independent of the battery voltage. Based on thrust measurement.

//#define ENABLE_THRUST_BAT_COMPENSATED


#define NBR_OF_MOTORS 4
// Motors IDs define
#define MOTOR_M1  0
#define MOTOR_M2  1
#define MOTOR_M3  2
#define MOTOR_M4  3

#ifdef CONFIG_TARGET_ESPLANE_V2_S2
    #define MOTOR3_GPIO  CONFIG_MOTOR01_PIN         // M1 for ESP32FC
    #define MOTOR4_GPIO  CONFIG_MOTOR02_PIN        // M2 for ESP32FC
    #define MOTOR1_GPIO  CONFIG_MOTOR03_PIN        // M3 for ESP32FC
    #define MOTOR2_GPIO  CONFIG_MOTOR04_PIN        // M4 for ESP32FC
#else
    #define MOTOR1_GPIO  CONFIG_MOTOR01_PIN         // M1 for ESP32FC
    #define MOTOR2_GPIO  CONFIG_MOTOR02_PIN        // M2 for ESP32FC
    #define MOTOR3_GPIO  CONFIG_MOTOR03_PIN        // M3 for ESP32FC
    #define MOTOR4_GPIO  CONFIG_MOTOR04_PIN        // M4 for ESP32FC
#endif

#define MOT_PWM_CH1  4      // Motor M1 pwmchannel
#define MOT_PWM_CH2  5      // Motor M2 pwmchannel
#define MOT_PWM_CH3  6      // Motor M3 pwmchannel
#define MOT_PWM_CH4  7      // Motor M4 pwmchannel     

// Test defines
#define MOTORS_TEST_RATIO         (uint16_t)(0.2*(1<<16))
#define MOTORS_TEST_ON_TIME_MS    50
#define MOTORS_TEST_DELAY_TIME_MS 150

// Sound defines
#define C4    262
#define DES4  277
#define D4    294
#define ES4   311
#define E4    330
#define F4    349
#define GES4  370
#define G4    392
#define AS4   415
#define A4    440
#define B4    466
#define H4    493
#define C5    523
#define DES5  554
#define D5    587
#define ES5   622
#define E5    659
#define F5    698
#define GES5  740
#define G5    783
#define AS5   830
#define A5    880
#define B5    932
#define H5    987
#define C6    1046
#define DES6  1108
#define D6    1174
#define ES6   1244
#define E6    1318
#define F6    1396
#define GES6  1479
#define G6    1567
#define AS6   1661
#define A6    1760
#define B6    1864
#define H6    1975
#define C7    2093
#define DES7  2217
#define D7    2349
#define ES7   2489
#define E7    2637
#define F7    2793
#define GES7  2959
#define G7    3135
#define AS7   3322
#define A7    3520
#define H7    3729
#define B7    3951

// Sound duration defines
#define EIGHTS 125
#define QUAD 250
#define HALF 500
#define FULL 1000
#define STOP 0

typedef enum {
    BRUSHED,
    BRUSHLESS
} motorsDrvType;

typedef struct {
    motorsDrvType drvType;

} MotorPerifDef;

/**
 * Motor mapping configurations
 */
//extern const MotorPerifDef* motorMapNoMotors[NBR_OF_MOTORS];
extern const MotorPerifDef *motorMapDefaultBrushed[NBR_OF_MOTORS];
//extern const MotorPerifDef* motorMapDefaltConBrushless[NBR_OF_MOTORS];
// extern const MotorPerifDef* motorMapBigQuadDeck[NBR_OF_MOTORS];
// extern const MotorPerifDef* motorMapBoltBrushless[NBR_OF_MOTORS];

/**
 * Test sound tones
 */
extern const uint16_t testsound[NBR_OF_MOTORS];
/*** Public interface ***/

bool pwm_timmer_init();
/**
 * Initialisation. Will set all motors ratio to 0%
 */
void motorsInit(const MotorPerifDef **motorMapSelect);
void arm_bldc(void);

/**
 * DeInitialisation. Reset to default
 */
void motorsDeInit(const MotorPerifDef **motorMapSelect);

/**
 * Test of the motor modules. The test will spin each motor very short in
 * the sequence M1 to M4.
 */
bool motorsTest(void);

/**
 * Set the PWM ratio of the motor 'id'
 */
void motorsSetRatio(uint32_t id, uint16_t ratio);

/**
 * Get the PWM ratio of the motor 'id'. Return -1 if wrong ID.
 */
int motorsGetRatio(uint32_t id);

/**
 * FreeRTOS Task to test the Motors driver
 */
void motorsTestTask(void *params);

/* Set PWM frequency for motor controller
 * This function will set all motors into a "beep"-mode,
 * each of the motor will turned on with a given ratio and frequency.
 * The higher the ratio the higher the given power to the motors.
 * ATTENTION: To much ratio can push your crazyflie into the air and hurt you!
 * Example:
 *     motorsBeep(true, 1000, (uint16_t)(72000000L / frequency)/ 20);
 *     motorsBeep(false, 0, 0); *
 * */
void motorsBeep(int id, bool enable, uint16_t frequency, uint16_t ratio);

#endif /* __MOTORS_H__ */

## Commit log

2025-10-21 Add ESC design files for 4-in-1 motor controller
    Includes complete Altium project files for the custom 4-in-1 Electronic Speed Controller (ESC), featuring schematic (.SchDoc), PCB layout (.PcbDoc), manufacturing files (Gerber, BOM, CPL), and design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
    [ESC_Schematic.SchDoc, MotorESC.PrjPcb, MotorESC_BOM.csv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]
2025-10-21 Add Flight Controller (FC) design files
    Contains complete Altium project files for the custom Flight Controller PCB, including schematic, layout, manufacturing outputs (Gerber, BOM, CPL), and design drawings. The FC integrates an ESP32 mic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
    [FC.PcbDoc, FC.PrjPcb, FC.SchDoc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]
2025-10-21 Update README with FC and ESC specifications and images
    Added detailed specifications and annotated images for the Flight Controller (FC) and Electronic Speed Controller (ESC) sections. Included descriptions of PCB design features, power regulation, senso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
2025-10-28 Added Ground Station Software

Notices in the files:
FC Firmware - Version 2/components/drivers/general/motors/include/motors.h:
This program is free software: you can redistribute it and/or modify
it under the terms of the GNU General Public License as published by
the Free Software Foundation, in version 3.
